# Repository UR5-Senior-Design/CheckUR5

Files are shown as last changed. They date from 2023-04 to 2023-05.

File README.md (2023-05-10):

# CheckUR5
## About
A Fall 2022 - Spring 2023 UTA Senior Design project that allows the UR5 collaborative robot arm to play a game of checkers with a human player.

Team CheckUR5:
- Nimita Uprety
- Patricia Rojas
- Hoang Ho
- Joanna Huynh
- Kevin Vu

Final demo video: https://www.youtube.com/watch?v=Sb-xevwk8ww

## Requirements
### Source Code
- [Main code](./main.py)
- [Arduino code](./arduino_magnet/arduino_magnet.ino)
- [Checkers code folder](./checkers)

### Physical Items
- UR5 collaborative robot arm
- Intel RealSense Depth Camera D435i
- 21 inch x 21 inch checkerboard
  - 0.5 inch border on each side
  - 2.5 inch x 2.5 inch squares
- 24 2 inch diameter [checker pieces](./designs/checker-piece-final.stl)
  - With washers or any magnetic material attached and ArUco markers on top
- Electromagnet gripper
  - Electromagnet circuit with Arduino Nano and MOSFET module
  - [Arduino code](./arduino_magnet/arduino_magnet.ino)
- Checker piece collection box

### Dependencies
- Linux distribution Ubuntu 22.04 LTS
- Python 3.x, we used 3.10.6
- OpenCV
- [RealSense SDK 2.0](https://dev.intelrealsense.com/docs/compiling-librealsense-for-linux-ubuntu-guide)
- [ur_rtde](https://pypi.org/project/ur-rtde/)
- pyserial

## Setup
Ensure the UR5 is connected to the same network as the PC that is running the code. Connect the camera and Arduino to SS USB ports.
- By default, the game uses `/dev/ttyUSB0/` as the Arduino port and `192.168.1.102` as the UR5's IP address. To change these, change line 26 in the [Game code](./checkers/game.py)

Movement logic of robot depends on its placement relative to the checkerboard and collection box. Each square's position is calculated based on the square designated as the top-left square and the distance difference between each square.

- To change where the top left square is, change `TOP_LEFT` in the [Robot code](./checkers/robot.py)
- To change where the collection box is, change `BOX_POS` in the [Robot code](./checkers/robot.py)

**The position values we used are based on the "Base" feature.**

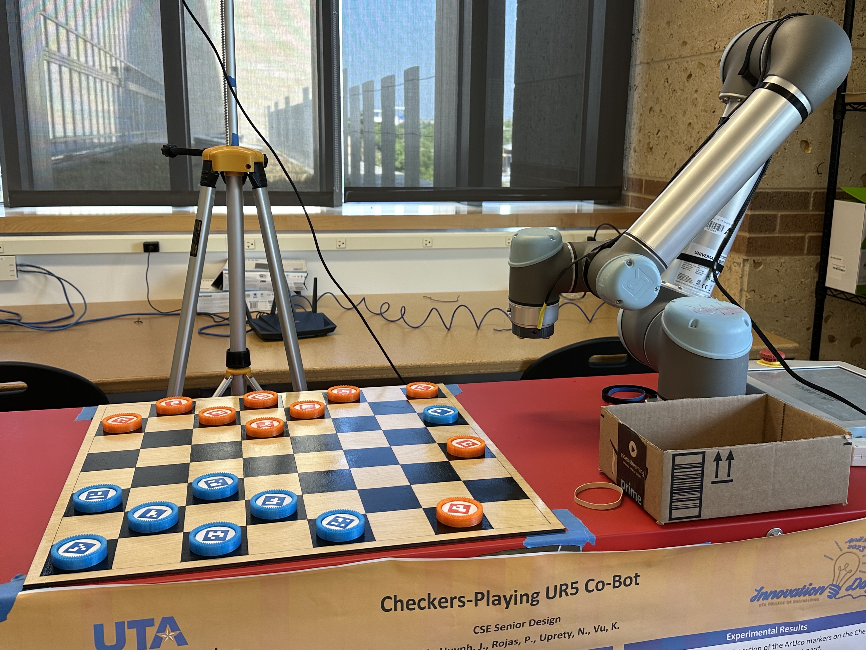
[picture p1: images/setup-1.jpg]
Project setup for playing checkers with the UR5 image 1

Project setup for playing checkers with the UR5 image 2
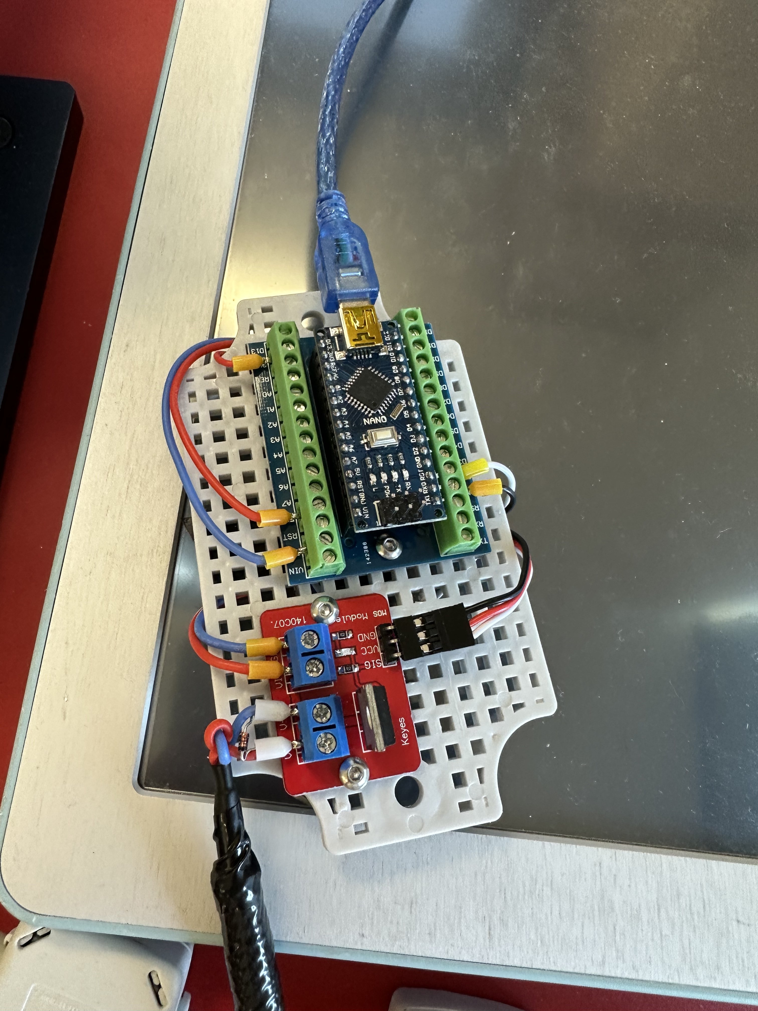
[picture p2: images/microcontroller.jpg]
The electromagnet circuit using the Arduino Nano and MOSFET module


## Playing the Game
1. Run [main.py](./main.py)
    - `python3 ./main.py`
2. Human player makes the first turn. Type `A` and press enter in the terminal to end the player's turn.
3. Enjoy!

## References
1. Techwithtim. (2020, September 3).“Techwithtim/Python-Checkers-AI/checkers: A checkers AI using the minimax algorithm.” Github, https://github.com/techwithtim/Python-Checkers-AI
2. Lindvig, A. P. (2022, October 31). Ur-rtde. PyPI. Retrieved April 7, 2023, from https://pypi.org/project/ur-rtde/ 
3. Söderby, K. (2023, March 9). Getting started with Arduino: Arduino documentation. Arduino Documentation | Arduino Documentation. Retrieved April 7, 2023, from https://docs.arduino.cc/learn/starting-guide/getting-started-arduino
4. UniversalRobots. (2012). Universal Robots User Manual Version 1.6. Universal Robots A/S.https://s3-eu-west-1.amazonaws.com/ur-support-site/17958/manual_en_UR5_CB2_1.6_US.pdf.

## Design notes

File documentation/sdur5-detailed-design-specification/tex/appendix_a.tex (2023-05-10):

% Include any additional documents (CAD design, circuit schematics, etc) as an appendix as necessary.
\subsection{CAD Models}
\begin{figure}[h!]
	\centering
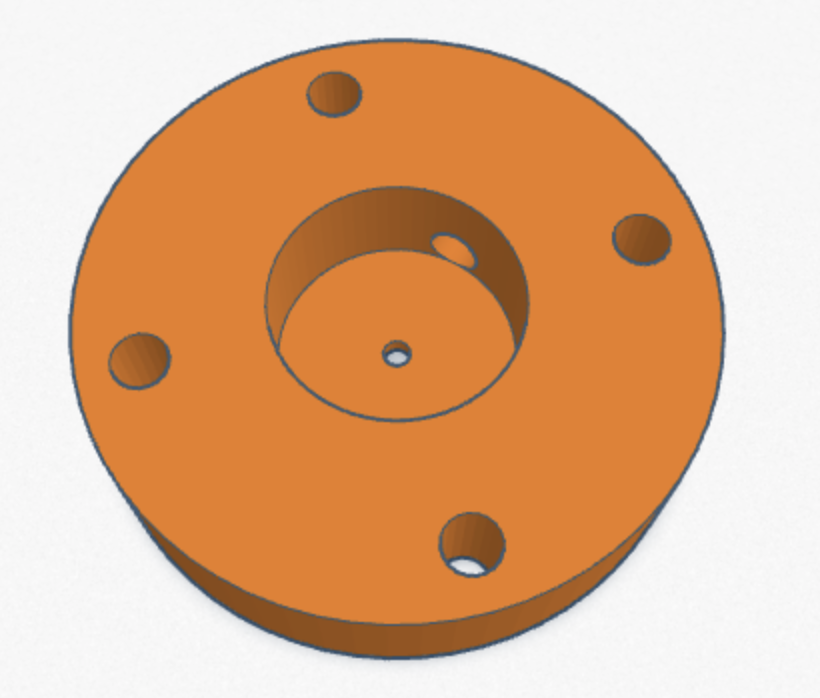
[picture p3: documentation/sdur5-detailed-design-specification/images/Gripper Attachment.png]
 	
 \caption{CAD Model of our Magnetic Gripper Attachment}
\end{figure}
\begin{figure}[h!]
	\centering
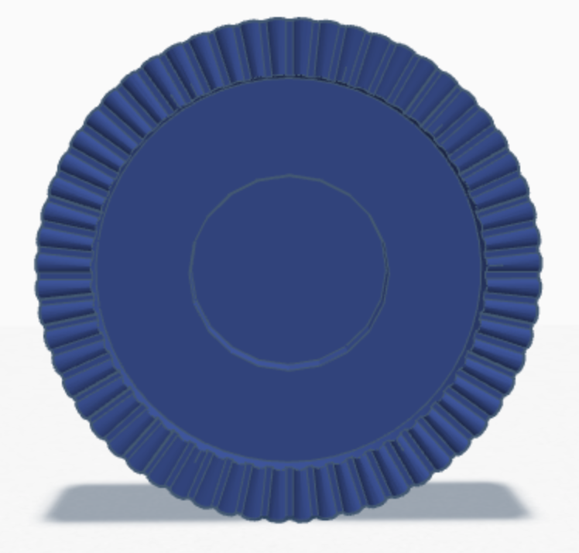
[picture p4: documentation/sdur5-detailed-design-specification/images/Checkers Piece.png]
 	
 \caption{CAD Model of our Regular Checkers Pieces}
\end{figure}
\begin{figure}[h!]
	\centering
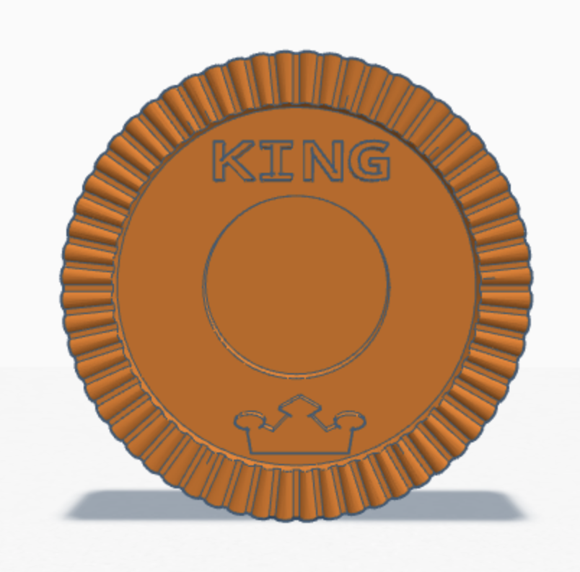
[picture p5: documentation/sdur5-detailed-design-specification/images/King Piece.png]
 	
 \caption{CAD Model of our King Checkers Pieces}
\end{figure}

\subsection{Circuit Schematics}
\begin{figure}[h!]
	\centering
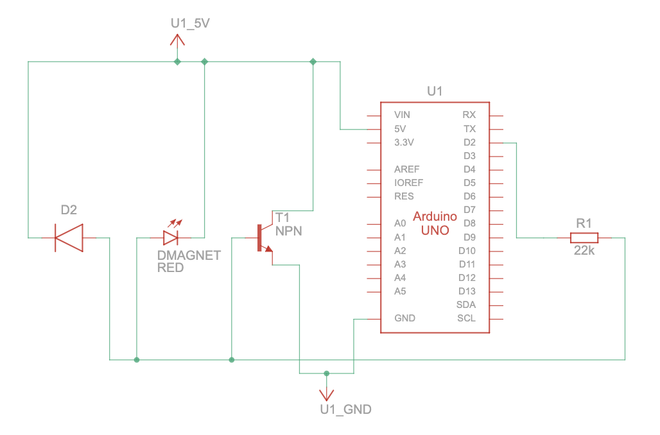
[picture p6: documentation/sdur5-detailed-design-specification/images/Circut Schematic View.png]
 	
 \caption{Schematic View of our Arduino \& Electromagnet setup}
\end{figure}
\begin{figure}[h!]
	\centering
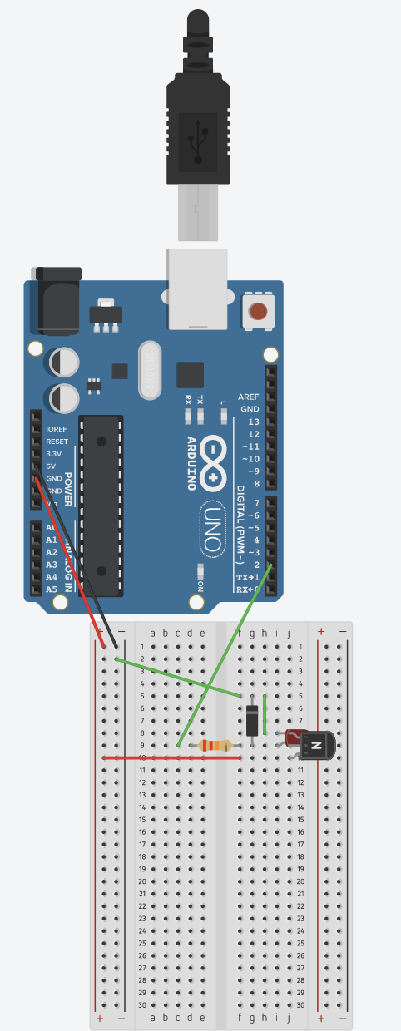
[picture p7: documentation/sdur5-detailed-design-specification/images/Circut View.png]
 	
 \caption{Circuit View of our Arduino \& Electromagnet setup}
\end{figure}

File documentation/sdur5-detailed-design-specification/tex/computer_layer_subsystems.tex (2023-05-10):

% In this section, the layer is described in terms of the hardware and software design. Specific implementation details, such as hardware components, programming languages, software dependencies, operating systems, etc. should be discussed. Any unnecessary items can be ommitted (for example, a pure software module without any specific hardware should not include a hardware subsection). The organization, titles, and content of the sections below can be modified as necessary for the project.
In this section, the Computer layer is described in detail. This layer consists of the HUD, GUI, and Software subsystems. Overall, the layer is responsible for communicating with the players information about the state of the game, sending the robot arm the actions it needs to take, and handling the decisions after each move.

\subsection{Layer Hardware}
% A description of any involved hardware components for the layer. For example, if each subsystem is a software process running on an embedded computer, discuss the specifics of that device here. Do not list a hardware component that only exists at the subsystem level (include it in the following sections).
The major hardware component of this layer is the computer itself. This computer is communicating to the UR5 robot arm through an Ethernet cable connected to the same router as the Ethernet cable connected to the UR5 control box. Additionally, as part of the computer, a monitor to display information to the player. A USB is also required to send to the Arduino the source code written to control the magnetic gripper.

\subsection{Layer Operating System}
% A description of any operating systems required by the layer.
The layer requires Linux distribution Ubuntu 22.04 LTS.

\subsection{Layer Software Dependencies}
% A description of any software dependencies (libraries, frameworks, etc) required by the layer.
 The layer will use the Python 3.10.6 programming language. It will also need to use the Arduino programming language to write the code to be executed on the Arduino that controls the magnetic gripper. Additionally, it is dependent on the Move Decision layer.

\subsection{HUD Subsystem}
% Descibe at a high level the purpose and basic design of this subsystem. Is it a piece of hardware, a class, a web service, or something else? Note that each of the subsystem items below are meant to be specific to that subystem and not a repeat of anything discussed above for the overall layer.
The Heads-Up Display (HUD) subsystem is a class that communicates with the Software subsystem of the Computer layer to receive information about the status of the game.The HUD subsystem displays to the user the status of the game and any information needed for the user. In this case the user is the Opponent layer. Information on the status of the game includes the current scores and a display of the game board on the computer monitor. This information is provided by the Software subsystem. Each time a player overtakes another player's checker piece, the score will be updated. When the physical game board changes, such as when a player moves a piece, this will also be reflected on the screen through the HUD.

\begin{figure}[h!]
	\centering
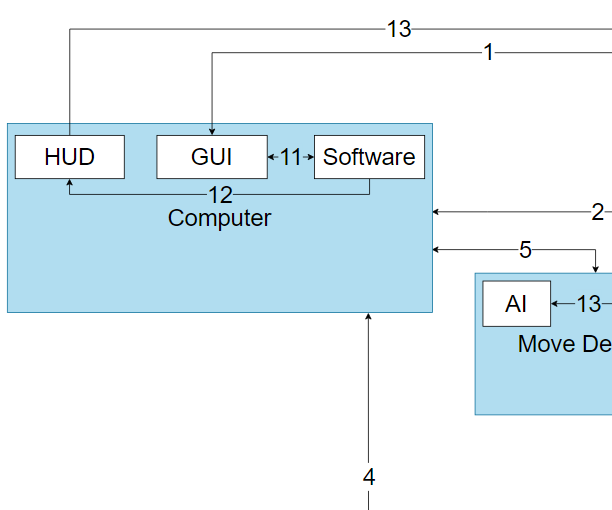
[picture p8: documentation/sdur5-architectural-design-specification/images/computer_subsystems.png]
 	
 \caption{Computer layer subsystems diagram}
\end{figure}

\subsubsection{Subsystem Hardware}
% A description of any involved hardware components for the subsystem.
A monitor connected to the computer to display game state status to the player.

% \subsubsection{Subsystem Operating System}
% A description of any operating systems required by the subsystem. removed because it is a repeat of things discussed above for the overall layer
% Linux distribution Ubuntu 22.04 LTS.

\subsubsection{Subsystem Software Dependencies}
% A description of any software dependencies (libraries, frameworks, design software for mechanical parts or circuits, etc) required by the subsystem.
This subsystem is dependent on the Software subsystem to receive information about the status of the game to display. It will also have software dependencies on GUI libraries such as PyQt5 or Tkinter.

\subsubsection{Subsystem Programming Languages}
% A description of any programming languages used by the subsystem.
The subsystem uses Python 3.10.6 as the programming language used.

\subsubsection{Subsystem Data Structures}
% A description of any classes or other data structures that are worth discussing for the subsystem. For example, data being transmitted from a microcontroller to a PC via USB should be first be assembled into packets. What is the structure of the packets?
N/A

\subsubsection{Subsystem Data Processing}
% A description of any algorithms or processing strategies that are worth discussing for the subsystem. If you are implementing a well-known algorithm, list it. If it is something unique to this project, discuss it in greater detail.
N/A

\subsection{GUI Subsystem}
% Descibe at a high level the purpose and basic design of this subsystem. Is it a piece of hardware, a class, a web service, or something else? Note that each of the subsystem items below are meant to be specific to that subystem and not a repeat of anything discussed above for the overall layer.
The Graphical User Interface (GUI) subsystem is a class that is the main interactive component between the Computer and Opponent layers. It communicates with the Software subsystem within the Computer layer for its inputs and outputs. The GUI displays buttons for the user (Opponent) to interact with. These buttons will be able to change the state of the game for purposes such as new game, restart game, and quit game. Each time the Opponent interacts with the GUI by clicking a corresponding button to a function, that button will send a mouse click signal for that button to the Software subsystem. This signals to the Software subsystem to execute the function associated with the button that is clicked. For example, if the user clicks a new game button, the software executes the processes needed to reset the state of the game and UR5 robot arm.

\subsubsection{Subsystem Hardware}
% A description of any involved hardware components for the subsystem.
A monitor connected to the computer to display the different options to the player. A mouse is also required for the player to interact with the GUI.

%\subsubsection{Subsystem Operating System}
% A description of any operating systems required by the subsystem. - removed because it is a repeat of things discussed above for the overall layer
% Linux distribution Ubuntu 22.04 LTS.

\subsubsection{Subsystem Software Dependencies}
% A description of any software dependencies (libraries, frameworks, design software for mechanical parts or circuits, etc) required by the subsystem.
This subsystem will have software dependencies on GUI libraries such as PyQt5 or Tkinter.

\subsubsection{Subsystem Programming Languages}
% A description of any programming languages used by the subsystem.
The subsystem uses Python 3.10.6 as the programming language used.

\subsubsection{Subsystem Data Structures}
% A description of any classes or other data structures that are worth discussing for the subsystem. For example, data being transmitted from a microcontroller to a PC via USB should be first be assembled into packets. What is the structure of the packets?
N/A

\subsubsection{Subsystem Data Processing}
% A description of any algorithms or processing strategies that are worth discussing for the subsystem. If you are implementing a well-known algorithm, list it. If it is something unique to this project, discuss it in greater detail.
N/A

\subsection{Software Subsystem}
% Descibe at a high level the purpose and basic design of this subsystem. Is it a piece of hardware, a class, a web service, or something else? Note that each of the subsystem items below are meant to be specific to that subystem and not a repeat of anything discussed above for the overall layer.
The Software subsystem is the main program for managing the checkers game itself and is behind the actions the UR5 Robot Arm will execute. This subsystem not only includes the source code itself, but also software packages needed for the program. The Software subsystem is responsible for handling events from the GUI. The subsystem also communicates with the UR5 robot arm through the Computer layer. The subsystem handles data on the status of the robot arm received from the robot arm itself. It also communicates to the robot arm what programmed actions it will need to perform. These actions will be determined by its interactions with the Move Decision layer which consists of the AI subsystem. The Software subsystem is also responsible for handling inputs from the Input Button/Device layer through the Computer layer.

\subsubsection{Subsystem Hardware}
% A description of any involved hardware components for the subsystem.
N/A

% \subsubsection{Subsystem Operating System}
% A description of any operating systems required by the subsystem. - removed because it is a repeat of things discussed above for the overall layer
%Linux distribution Ubuntu 22.04 LTS.

\subsubsection{Subsystem Software Dependencies}
% A description of any software dependencies (libraries, frameworks, design software for mechanical parts or circuits, etc) required by the subsystem.
The Software subsystem requires the ur\_rtde interface library to communicate with the UR5 robot arm. This library will allow us to write Python code to receive data from the UR5, and also control it. This is done using the RTDE Receive Interface API and RTDE Control Interface API from the library respectively. Documentation for the library can be found here: https://sdurobotics.gitlab.io/ur\_rtde/index.html. Controlling the UR5 includes communicating with the Move Execution layer and sending the commands to move the robot arm to a certain position. The subsystem is dependent on the Computer Vision and AI subsystems from the Move Decision layer to determine the commands it needs to send to the robot arm. It also needs this dependency to manage the checkers game and send the data required by the HUD subsystem. Moreover, it is also dependent on the GUI subsystem and Input Button/Device layer to listen to events from the player and handle them for the checkers game accordingly.

\subsubsection{Subsystem Programming Languages}
% A description of any programming languages used by the subsystem.
The subsystem uses Python 3.10.6 as the programming language used.

\subsubsection{Subsystem Data Structures}
% A description of any classes or other data structures that are worth discussing for the subsystem. For example, data being transmitted from a microcontroller to a PC via USB should be first be assembled into packets. What is the structure of the packets?
N/A

\subsubsection{Subsystem Data Processing}
% A description of any algorithms or processing strategies that are worth discussing for the subsystem. If you are implementing a well-known algorithm, list it. If it is something unique to this project, discuss it in greater detail.
N/A

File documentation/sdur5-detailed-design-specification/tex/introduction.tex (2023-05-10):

% Your introduction should provide a brief overview of the product concept and a reference to the requirement specification and architectural design documents in 1 or 2 paragraphs. The purpose is to provide the reader with the location of relevant background material that lead to the design details presented in this document.

The UR5 co-bot will be programmed to be able to play the interactive \& strategy-based game, checkers, against a human opponent. The robot will have an electropermanent magnetic attachment that will allow it to pick up and move the individual checkers pieces. The robot is not intended to beat the human opponent every time but rather just have the ability to play a full game of checkers against them. Our project aims to showcase the UR5 co-bot's abilities as a means of promoting the UT Arlington College of Engineering to prospective students through the means of an interactive demonstration.

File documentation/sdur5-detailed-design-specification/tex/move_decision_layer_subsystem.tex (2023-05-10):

 %In this section, the layer is described in terms of the hardware and software design. Specific implementation details, such as hardware components, programming languages, software dependencies, operating systems, etc. should be discussed. Any unnecessary items can be ommitted (for example, a pure software module without any specific hardware should not include a hardware subsection). The organization, titles, and content of the sections below can be modified as necessary for the project.
 In this section, we describe the move decision layer in detail. This layer consists of Artificial Intelligence and Computer Vision. Overall, this layer is responsible for one of the most important parts of this project that is the decision making process of the UR5 robot for the Checkers game. This does so by determining what commands to send to the robot arm.

\subsection{Layer Hardware}
%A description of any involved hardware components for the layer. For example, if each subsystem is a software process running on an embedded computer, discuss the specifics of that device here. Do not list a hardware component that only exists at the subsystem level (include it in the following sections).
This layer requires the computer to utilize artificial intelligence and computer vision aspects of the decision making.

\subsection{Layer Operating System}
%A description of any operating systems required by the layer.
The layer requires Linux distribution Ubuntu 22.04 LTS.

\subsection{Layer Software Dependencies}
%A description of any software dependencies (libraries, frameworks, etc) required by the layer.
The layer will use the Python 3.10.6 programming language. 

\subsection{Artificial Intelligence}
%Descibe at a high level the purpose and basic design of this subsystem. Is it a piece of hardware, a class, a web service, or something else? Note that each of the subsystem items below are meant to be specific to that subystem and not a repeat of anything discussed above for the overall layer.
The Artificial Intelligence communicates with the camera and Computer layer subsystems to make decisions for the UR5 robot arm.

\begin{figure}[h!]
	\centering
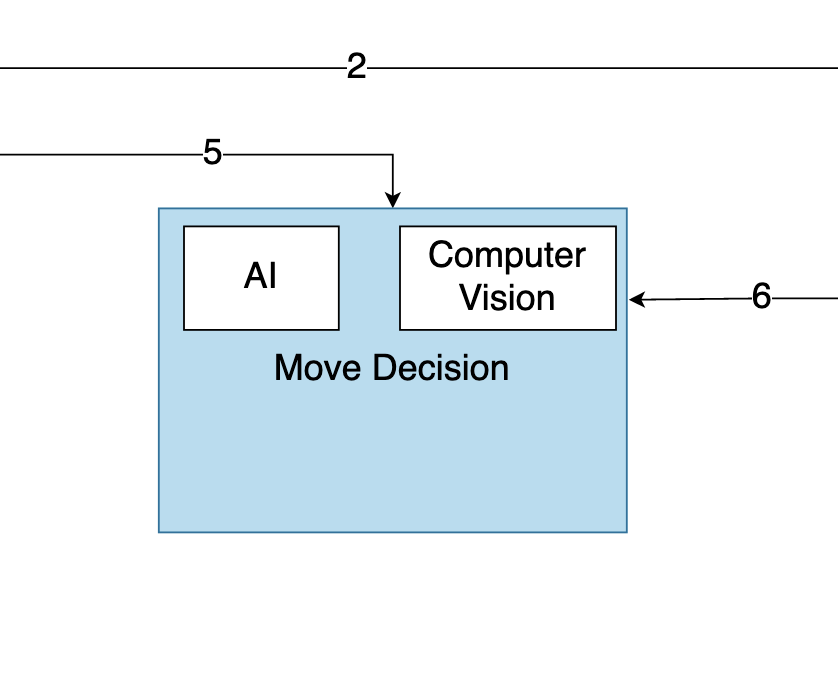
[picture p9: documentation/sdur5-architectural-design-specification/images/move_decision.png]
 	
 \caption{Example subsystem description diagram}
\end{figure}

\subsubsection{Subsystem Hardware}
%A description of any involved hardware components for the subsystem.
This subsystem requires the computer to utilize artificial intelligence aspect of the decision making.

\subsubsection{Subsystem Operating System}
%A description of any operating systems required by the subsystem.
The subsystem requires Linux distribution Ubuntu 22.04 LTS.

\subsubsection{Subsystem Software Dependencies}
%A description of any software dependencies (libraries, frameworks, design software for mechanical parts or circuits, etc) required by the subsystem.
The subsystem will use python libraries designed for artificial intelligence.

\subsubsection{Subsystem Programming Languages}
%A description of any programming languages used by the subsystem.
This subsystem will use the Python 3.10.6 programming language.

\subsubsection{Subsystem Data Structures}
%A description of any classes or other data structures that are worth discussing for the subsystem. For example, data being transmitted from a microcontroller to a PC via USB should be first be assembled into packets. What is the structure of the packets?
N/A

\subsubsection{Subsystem Data Processing}
%A description of any algorithms or processing strategies that are worth discussing for the subsystem. If you are implementing a well-known algorithm, list it. If it is something unique to this project, discuss it in greater detail.
N/A

\subsection{Computer Vision}
%Descibe at a high level the purpose and basic design of this subsystem. Is it a piece of hardware, a class, a web service, or something else? Note that each of the subsystem items below are meant to be specific to that subystem and not a repeat of anything discussed above for the overall layer.
The Computer Vision interacts with the frames received from the camera to determine the player's move.

% \begin{figure}[h!]
% 	\centering
%  	\includegraphics[width=0.60\textwidth]{images/subsystem}
%  \caption{Example subsystem description diagram}
% \end{figure}

\subsubsection{Subsystem Hardware}
%A description of any involved hardware components for the subsystem.
The subsystem will be using a camera to receive frames of the checkers position for both the players and will also use the computer for the computer vision process.

\subsubsection{Subsystem Operating System}
%A description of any operating systems required by the subsystem.
N/A

\subsubsection{Subsystem Software Dependencies}
%A description of any software dependencies (libraries, frameworks, design software for mechanical parts or circuits, etc) required by the subsystem.
This subsystem will use OpenCV and NumPy for the software dependencies.

\subsubsection{Subsystem Programming Languages}
%A description of any programming languages used by the subsystem.
This subsystem will use the Python 3.10.6 programming language.

\subsubsection{Subsystem Data Structures}
%A description of any classes or other data structures that are worth discussing for the subsystem. For example, data being transmitted from a microcontroller to a PC via USB should be first be assembled into packets. What is the structure of the packets?
N/A

\subsubsection{Subsystem Data Processing}
%A description of any algorithms or processing strategies that are worth discussing for the subsystem. If you are implementing a well-known algorithm, list it. If it is something unique to this project, discuss it in greater detail.
N/A

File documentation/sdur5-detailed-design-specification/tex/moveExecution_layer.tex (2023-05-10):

In this section, we describe the move execution layer. This layer is responsible for one of the key functionalities of our project which is the UR5 Robotic Arm's movement, which allows for the checkers game to take place between the user and the co-bot. The move execution layer is made up of three subsystems, the UR5 Robot Arm itself, the electromagnetic gripper, as well as an Arduino.

\subsection{Layer Hardware}
In terms of the Move Execution Layer the most heavily involved hardware component for this layer is the UR5 robotic arm itself. 

\subsection{Layer Operating System}
This layer utilizes Robot Operating System (ROS), although we do not primarily use ROS as we are primarily using Python to move our co-bot. ROS will be utilized to check the status of our robot's arm movements/coordinates at any given time.

\subsection{Layer Software Dependencies}
This layer will also utilize the Python 3.10.6 programming language. 

\begin{figure}[h!]
	\centering
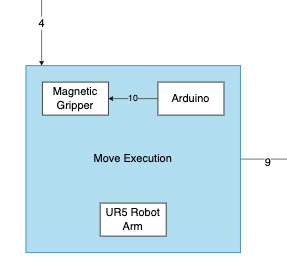
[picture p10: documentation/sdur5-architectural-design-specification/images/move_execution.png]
 	
 \caption{Move Execution subsystem description diagram}
\end{figure}

\subsection{UR5 Robot Arm}

The UR5 co-bot arm must be able to follow the instructions as asked by the software in order to hover over the correct location on the checker board. The robot must be able to move to fixed locations as predetermined by ROS and our custom software in order to not only move to specified pieces on the board but also to the collection box, and a waiting position.

The UR5 co-bot arm is responsible for the main mechanics of our project. As its ability to move to move to a spot on the board and pick up a piece and move it to another position is necessary so that the UR5 can play against its human oppponent.

\subsubsection{Subsystem Hardware}
In the UR5 Subsystem as well as the Move Execution Layer, the hardware component involved is the UR5 robotic arm itself.

\subsubsection{Subsystem Operating System}
The operating system required here is ROS.

\subsubsection{Subsystem Software Dependencies}
This subsystem layer will require a Universal Robots Python library so that we can control the co-bots movements through python scripts. The Python library we intend on using for this is ur\_rtde.

\subsubsection{Subsystem Programming Languages}
The UR5 subsystem requires the Python 3.10.6 programming language.

\subsubsection{Subsystem Data Structures}
The pre-recorded coordinates of our robot's movements will be saved into a multi-dimensional array so that our robot will have a list of saved positions to go to. The decision on where to go is determined by our Move Decision layer.

\subsubsection{Subsystem Data Processing}
N/A

\subsection{Magnetic Gripper}
The Magenetic subsystem of our Move Execution Layer is responsible for the UR5 robotic arm's ability to "pick-up" each checkers piece. This subsystem is integral to the project as a whole because without it the pieces will not be moved and the checkers game cannot be played.

\subsubsection{Subsystem Hardware}
This subsystem requires more hardware components than some of our other subsystems. It consists of an Arduino, an electromagnet, transistor NPN(2N3904), diode(1N4148), 22K Ω resistor, wires, breadboard, as well as a 3D printed attachement so that it can be screwed into the UR5 arm.

\subsubsection{Subsystem Operating System}
N/A

\subsubsection{Subsystem Software Dependencies}
This subsystem layer requires the Arduino 2.0.3 IDE. As that is needed for us to provide python scripts to Arduino which in turn will power our electromagnet.

\subsubsection{Subsystem Programming Languages}
The UR5 subsystem requires the Python 3.10.6 programming language.

N/A

\subsubsection{Subsystem Data Processing}
N/A

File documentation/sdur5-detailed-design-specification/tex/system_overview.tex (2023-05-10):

% This section should reintroduce the full data flow diagram from the architectural specification, and discuss at a high level the purpose of each layer. You do not need to include a subsection for each layer, a 1 - 2 paragraph recap is sufficient.
\begin{flushleft}
The system for our product is currently simplified into 4 layers and 3 high-level components. Each layer/component will interact with one another in different ways.
\end{flushleft}
\begin{flushleft}
The Opponent is the person that will be going against the robot during the checkers game. The Input Device is one of the ways the opponent will be able to facilitate the progression of the checkers match. The camera is the component that acts as the eyes into the real world for our system. The Move Decision layer is the layer that will make all of the move decisions that the robot will make. This layer consists of Computer Vision and AI. The Computer layer is the central piece of our system. This layer acts as the facilitator of the checkers match, and receives input from the Opponent to progress the match, sends signals to the AI layer to grab board state and make a move, and signals the UR5 Robot Arm layer to execute those moves. The Move Execution layer is the layer that will physically execute the moves that our system will make during a checkers match with the robot arm and related parts. And finally, The External Components layer is composed of all of the physical checkers board game pieces. Both the Opponent component and the Move Execution layer physically interact with the External Components layer when they have made their move decisions to progress the match.
\end{flushleft}

\begin{figure}[h!]
	\centering
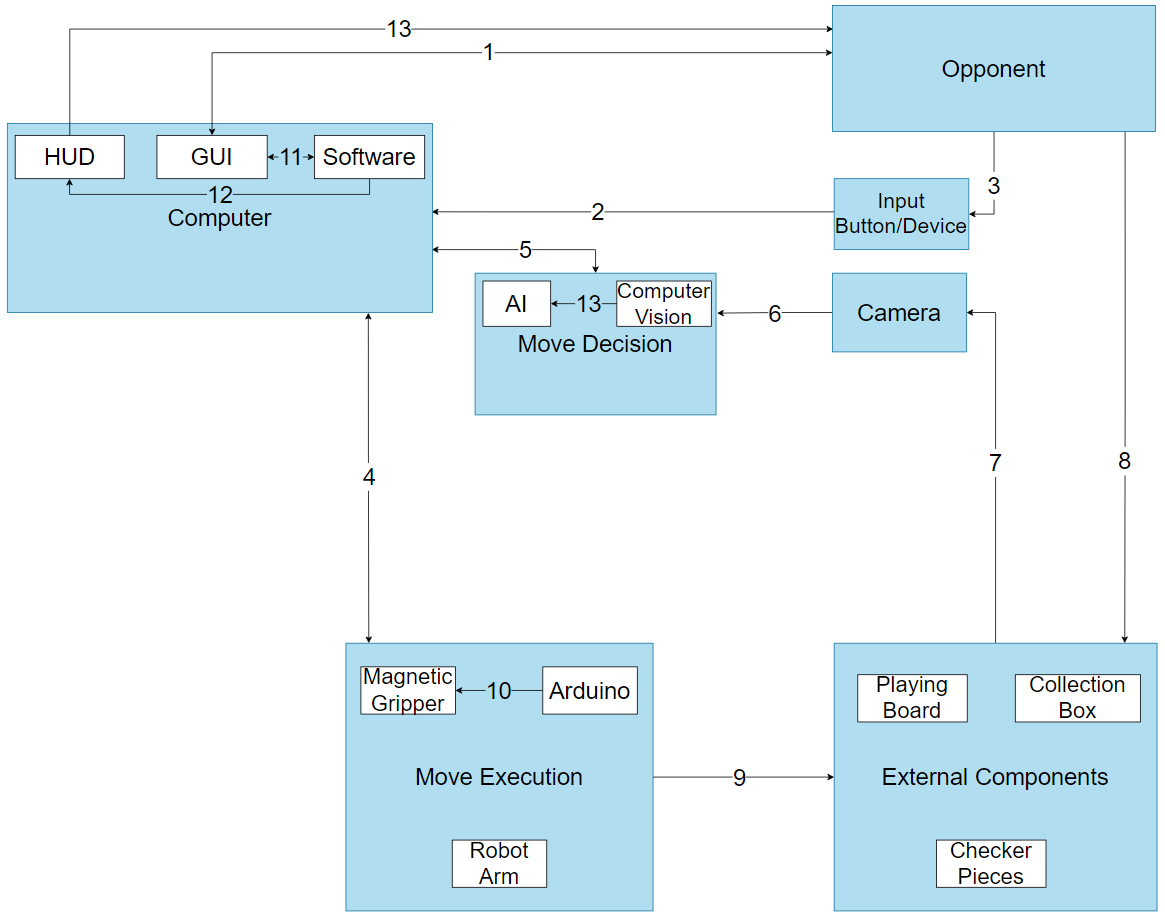
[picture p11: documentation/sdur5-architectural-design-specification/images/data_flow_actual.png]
 	
 \caption{System architecture}
\end{figure}

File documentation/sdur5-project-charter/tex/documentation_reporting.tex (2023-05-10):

%%% In this section, you will describe all of the various artifacts that you will generate and maintain during the project life cycle. Describe the purpose of each item below, how the content will be generated, where it will be stored, how often it will be updated, etc. Replace the default text for each section with your own description. Reword this paragraph as appropriate.

\subsection{Major Documentation Deliverables}
\subsubsection{Project Charter}
The project charter is intended to communicate Team UR5's understanding and research on the project. It is the current list of commitments the team will be making. The initial version of the document will be delivered October 3, 2022. The final version will be delivered during the second semester in May 2023. This document will be maintained and updated after every sprint as needed, and when the sponsor approves of these changes.

% Describe how this document will be maintained and updated (how often, under what circumstances, etc.). When will the initial version be delivered? When will the final version be delivered?
https://www.overleaf.com/project/631b8af69f1ea6c375d502b0
\subsubsection{System Requirements Specification}
The Systems Requirements Specification will be maintained and updated during every sprint as features are added or with further understanding of the technology. The initial version of this document will be delivered October 24, 2022. The final version will be delivered during the second semester in May 2023.

% Describe how this document will be maintained and updated (how often, under what circumstances, etc.). When will the initial version be delivered? When will the final version be delivered?

\subsubsection{Architectural Design Specification}
The Architectural Design Specification will be maintained and updated as needed during every sprint especially when there are changes in design or clarifications. The initial version of this document will be delivered November 14, 2022. The final version will be delivered during the second semester in May 2023.

% Describe how this document will be maintained and updated (how often, under what circumstances, etc.). When will the initial version be delivered? When will the final version be delivered?

\subsubsection{Detailed Design Specification}
The Detailed Design Specification will be maintained and updated as needed during every sprint especially when there are changes in design or clarifications. The initial version of this document will be delivered within the first quarter of 2023. The final version will be delivered during the second semester in May 2023.

% Describe how this document will be maintained and updated (how often, under what circumstances, etc.). When will the initial version be delivered? When will the final version be delivered?

\subsection{Recurring Sprint Items}
\subsubsection{Product Backlog}
Items will be added to the product backlog as the System Requirements Specification document is updated. These items will be prioritized based on customer needs and feasibility of the requirement for the current point in time. Team vote and feedback will also be taken into consideration. Jira Software by Atlassian will be used to maintain and work collaboratively on the product backlog.

% How will items be added to the product backlog from the SRS? How will these items be prioritized? Who makes the decision (product owner, group vote, etc.)? What software will be used to maintain and share the product backlog with team members and stakeholders?

\subsubsection{Sprint Planning}
Each sprint will be planned based on documentation and feature implementation deadlines. Team meetings will be held after each sprint to determine the sprint goals. There will be 4 sprints for the first semester and 4 sprints for the second semester, totalling 8 sprints for both semesters.

% How will each sprint plan be planned? How many sprints will there be (you need to look at the schedules for this course and previous Senior Design II courses during the appropriate semesters to figure this out).

\subsubsection{Sprint Goal}
The team will meet and discuss sprint goals. These sprint goals will be decide as a team. Our customer Christopher McMurrough will be involved in the process as needed through scheduled meetings.

% Who decides the sprint goal? How will you involve your customer in this process?

\subsubsection{Sprint Backlog}
Team discussion will be held to determine which product backlog items will make their way into the sprint backlog. The backlog will be maintained using Jira Software developed by Atlassian.

% Who decides which product backlog items make their way into the sprint backlog? How will the backlog be maintained (collaboration software, a "scrum board", etc.)?

\subsubsection{Task Breakdown}
Each team member will voluntarily claim a task, otherwise it will be random. Time spent on tasks will be documented using Jira Software.

% How will individual tasks be assigned from the sprint backlog? Will it be up to each team member to voluntarily claim a task, or will it come from the product owner? How will time spent on tasks be documented?

\subsubsection{Sprint Burn Down Charts}
The burn down charts will allow the team to track the progress of the project. Currently, using Jira Software will automatically generate the burn down charts for each sprint. Each individual team member is responsible for manually updating the effort and time spent as they complete each assigned task. Jira Software will also be able to access all of this. In addition to the Jira log, Microsoft Excel will be used to manually create the burn down charts in case members don't update on Jira. See Figure 2 and 3 for examples.

\begin{figure}[h!]
    \centering
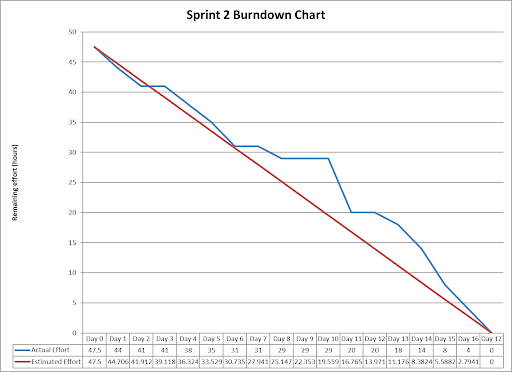
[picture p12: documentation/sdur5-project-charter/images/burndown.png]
    
    \caption{Example sprint burn down chart}
\end{figure}

\begin{figure}[h!]
    \centering
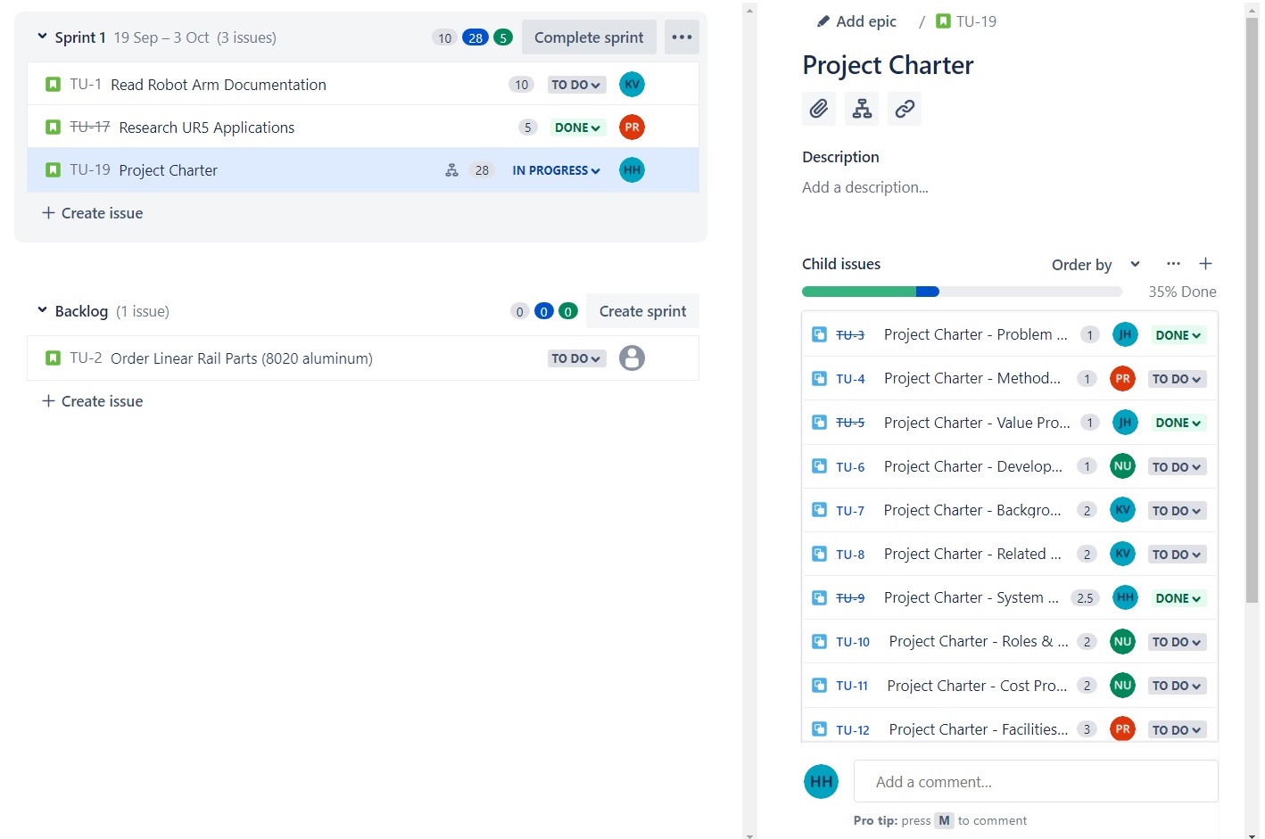
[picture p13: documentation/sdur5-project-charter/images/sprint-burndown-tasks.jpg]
    
    \caption{Example task tracking}
\end{figure}

% Who will be responsible for generating the burn down charts for each sprint? How will they be able to access the total amount of effort expended by each individual team member? What format will the burn down chart use (include an example burn down chart below).

\subsubsection{Sprint Retrospective}
The sprint retrospective will be handled as a team during team meetings. This discussion will happen after each sprint review presentation at the end of each sprint. What went well, and what is needed to be adjusted will be documented as a team before the next sprint plan meeting.

% How will the sprint retrospective be handled as a team? When will this discussion happen after each sprint? What will be documented as a group and as individuals, and when will it be due?

\subsubsection{Individual Status Reports}
Each individual member will primarily report the tasks assigned to them and the time spent on each task for each sprint. Individuals can also include in their report any concerns or issues that may be addressed for future sprints.

% What sort of status will be reported by each individual member, and how often will it be reported? What key items will be contained in the report?

\subsubsection{Engineering Notebooks}
%%% notes, status reports, budgeting, sprint info
% The engineering notebook may contain any project notes, status reports, budgeting, sprint information, etc. It will be updated every week by each team member at minimum. The minimum amount of pages that will be completed will be 1 page for each sprint period. These sprint periods are around 2 weeks long. Any team member that is not the author will sign as a "witness" for each page.

% How often will the engineering notebook be updated, at a minimum, by each team member? What is the minimum amount of pages that will be completed for each interval, and how long will that interval be? How will the team keep each member accountable? Who will sign of as a "witness" for each ENB page?

\subsection{Closeout Materials}
\subsubsection{System Prototype}
Included in the final system prototype will be all major components (computer software, UR5, sensors, checkerboard, etc.) to demonstrate a game with the UR5.

% What will be included in the final system prototype? How and when will this be demonstrated? Will there be a Prototype Acceptance Test (PAT) with your customer? Will anything be demonstrated off-site? If so, will there be a Field Acceptance Test (FAT)?

\subsubsection{Project Poster}
Included on the project poster will be an overview, methodology and design, and results. Poster dimensions will be 32 inches tall by 40 inches wide.

% What will be included on the poster, what will be the final dimensions, and when will it be delivered?

% \subsubsection{Web Page}
% The project web page will have the project's overview, design, results, and document deliverables. The web page will be accessible to the public. When the web page will be delivered and updated is still to be decided.

% What will be included on the project web page? Will it be accessible to the public? When will this be delivered? Will it be updated throughout the project, or just provided at closeout (at a minimum, you need to provide a simple web page at the end).

\subsubsection{Demo Video}
Shown in the demo video will be the robot playing a game with a human. B-reel footage will be recorded throughout project implementation to show progress and different features.

% What will be shown in the demo video(s)? Will you include a B-reel footage for future video cuts? Approximately how long will the video(s) be, and what topics will be covered?

\subsubsection{Source Code}
The source code will be maintained on GitHub using the Git version control system. The source code will also be publicly available to the customer through GitHub. License terms are still to be decided, but still likely be listed in a single ReadMe file.

% How will your source code be maintained? What version control system will you adopt? Will source code be provided to the customer, or binaries only? If source code is provided, how will it be turned over to the customer? Will the project be open sourced to the general public? If so, what are the license terms (GNU, GPL, MIT, etc.). Where will the license terms be listed (in each source file, in a single readme file, etc.).

\subsubsection{Source Code Documentation}

The team plans to write a README for documentation and setup instructions for future users. The team also plans to potentially look into using Doxygen or Pydocs to generate the documentation. The format of the final documentation is still to be decided, however it is likely it will provided as a PDF or HTML file.

% The team plans to look into using Doxygen or Pydocs to generate the documentation. The format of the final documentation is still to be decided, however it is likely it will provided as a PDF or HTML file.

% What documentation standards will be employed? Will you use tools to generate the documentation (Doxygen, Javadocs, etc.). In what format will the final documentation be provided (PDF, browsable HTML, etc.)?

\subsubsection{Hardware Schematics}
The project will involve the UR5 Robot Arm. This robot arm will need a gripper for picking up pieces. In addition to that, a camera will be needed for the robot to detect the state of the game board, determine its next move, and move its pieces. The rest of the project involves python scripts.

% Will you be creating printed circuit boards (PCBs) or wiring components together? If so, list each applicable schematic and what sort of data it will contain (PCB layout, wiring diagram, etc.). If your project is purely software, omit this section.

\subsubsection{CAD files}
The project will need custom checker pieces if the UR5 plans to use a magnetic gripper to pick up the pieces. The FabLab at UTA has software support for SketchUp, Meshmixer, Tinkercad, Fusion 360, and SolidWorks. Currently, the plan is to use the free, online 3D modeling program Tinkercad to make the pieces. Blender could also be another free option to use outside of the software supported in the FabLab. The CAD files will be saved in STL file format to work with the 3D printers available in the FabLab at UTA.

% Will the project involve any mechanical design, such as 3D printed or laser-cut parts? If so, what software will you use to generate the files and what file formats will you provide in your closeout materials (STL, STEP, OBJ, etc.). If your project is purely software, omit this section.

\subsubsection{Installation Scripts}
There are currently no plans to provide installation scripts. At the moment, instructions are planned to be found in the ReadMe file on the GitHub repository.

% How will the customer deploy software to new installations? Will you provide installation scripts, install programs, or any other tools to improve the process? Will there be multiple scripts provided (perhaps separate scripts for the graphical front end and back end server software)? 

% \subsubsection{User Manual}
% A digital user manual will be provided for the customer. This digital user manual can also be printed.

% Will you customer need a printed or digital user manual? Will they need a setup video? Decide now what will be provided and discuss.

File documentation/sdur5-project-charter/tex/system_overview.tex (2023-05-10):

The UR5 co-bot will be able to play a game of checkers against a human opponent. In order for the robot to do this, the robot arm will need a gripper and a camera. The gripper will be needed to pick up checker pieces. This gripper could be magnetic or a suction cup. In the case of a magnetic gripper, the checker pieces themselves will need to also be magnetic. The robot arm will also need to be paired with a camera in order to see and detect the checkerboard and its pieces. This is so the robot arm can determine the current state of the game, and determine the next optimal move for a piece to take. The computer will communicate with the robot arm and issue commands for it to make a particular move. Shown in Figure 1 is a high-level view of the implementation.

\begin{figure}[h!]
    \centering
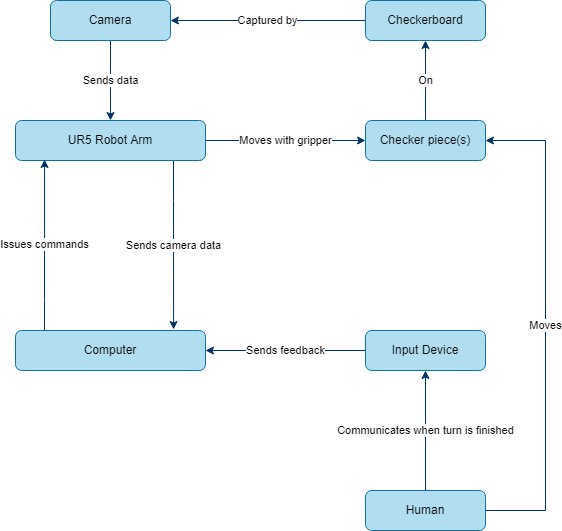
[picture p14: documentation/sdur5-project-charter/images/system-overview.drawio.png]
    
    \caption{System Overview}
\end{figure}

As is illustrated in Figure 1, when the human player makes a move, the human must use some input device to communicate to the computer that they have completed their turn and it is now the UR5's turn to make a move. This input device could be a simple external button, or the computer keyboard. The computer is responsible for being the interface that communicates with the robot arm on what move it should make, how it should move, and any other commands needed to control it. Additionally, the computer will process the data received from the camera on the robot arm utilizing computer vision.

% Explain, at a high level, how you will implement a solution to the problem. Include a diagram of major components to the system (not a full architectural design, but a high level overview of the major system components and how a user or external system might interface). Avoid specific implementation details (operating system, programming languages, etc.). This section should occupy at least 1 full page.

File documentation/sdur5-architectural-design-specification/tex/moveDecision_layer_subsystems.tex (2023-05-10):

%In this section, the layer is described in some detail in terms of its specific subsystems. Describe each of the layers and its subsystems in a separate chapter/major subsection of this document. The content of each subsystem description should be similar. Include in this section any special considerations and/or trade-offs considered for the approach you have chosen.
In this section, we describe the move decision layer. This layer is responsible for the decision making process of the UR5 robot for the Checkers game.
\subsection{Artificial Intelligence}
%This section should be a general description of a particular subsystem for the given layer. For most subsystems, an extract of the architectural block diagram with data flows is useful. This should consist of the subsystem being described and those subsystems with which it communicates.
The Artificial Intelligence communicates with the camera and Computer layer subsystems to make decisions for the UR5 robot arm.
\begin{figure}[h!]
	\centering
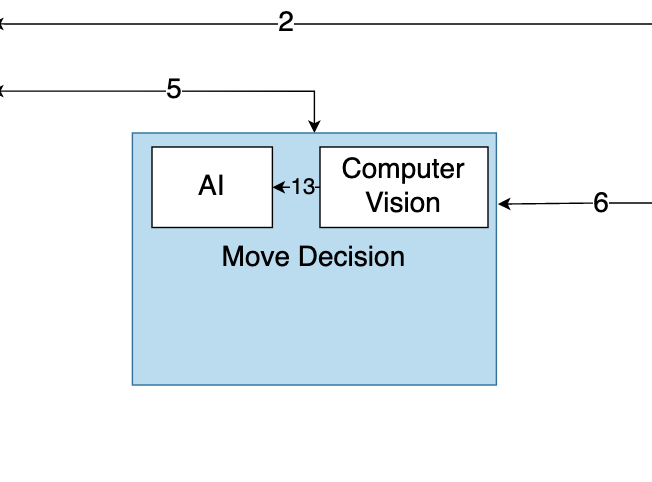
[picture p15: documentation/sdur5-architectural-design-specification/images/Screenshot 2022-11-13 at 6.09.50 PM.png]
 	
 \caption{Move decision layer subsystems diagram}
\end{figure}

\subsubsection{Assumptions}
%Any assumptions made in the definition of the subsystem should be listed and described. Pay particular attention to assumptions concerning interfaces and interactions with other layers.
N/A

\subsubsection{Responsibilities}
%Each of the responsibilities/features/functions/services of the subsystem as identified in the architectural summary must be expanded to more detailed responsibilities. These responsibilities form the basis for the identification of the finer-grained responsibilities of the layer's internal subsystems. Clearly describe what each subsystem does.
The Artificial Intelligence calculates the next move for the Computer. It compares the best move by looking at the next two to three steps ahead by the appropriate algorithm. It also determines any invalid moves by the player.  

\subsubsection{Artificial Intelligence Interfaces}
%Each of the inputs and outputs for the subsystem are defined here. Create a table with an entry for each labelled interface that connects to this subsystem. For each entry, describe any incoming and outgoing data elements will pass through this interface.
Details in Table 5 show the incoming and outgoing data elements.
\begin {table}[H]
\caption {Subsystem interfaces} 
\begin{center}
    \begin{tabular}{ | p{1cm} | p{6cm} | p{3cm} | p{3cm} |}
    \hline
    ID & Description & Inputs & Outputs \\ \hline
    \#5 & Signal from the computer & \pbox{3cm}{N/A} & \pbox{3cm}{N/A}  \\ \hline
    \end{tabular}
\end{center}
\end{table}

\subsection{Computer Vision}
%This section should be a general description of a particular subsystem for the given layer. For most subsystems, an extract of the architectural block diagram with data flows is useful. This should consist of the subsystem being described and those subsystems with which it communicates.
The Computer Vision interacts with the frames received from the camera to determine the player's move.

\subsubsection{Assumptions}
%Any assumptions made in the definition of the subsystem should be listed and described. Pay particular attention to assumptions concerning interfaces and interactions with other layers.
N/A

\subsubsection{Responsibilities}
%Each of the responsibilities/features/functions/services of the subsystem as identified in the architectural summary must be expanded to more detailed responsibilities. These responsibilities form the basis for the identification of the finer-grained responsibilities of the layer's internal subsystems. Clearly describe what each subsystem does.
It successfully identifies the movements of the Checkers pieces. It also identifies the current locations on the Checkers board.

\subsubsection{Subsystem Interfaces}
%Each of the inputs and outputs for the subsystem are defined here. Create a table with an entry for each labelled interface that connects to this subsystem. For each entry, describe any incoming and outgoing data elements will pass through this interface.
Details in Table 6 show the incoming and outgoing data elements.
\begin {table}[H]
\caption {Computer Vision interfaces} 
\begin{center}
    \begin{tabular}{ | p{1cm} | p{6cm} | p{3cm} | p{3cm} |}
    \hline
    ID & Description & Inputs & Outputs \\ \hline
   \#13 & Send input to Artificial Intelligence & \pbox{3cm}{Computer Vision input} & \pbox{3cm}{Checkers Move}  \\ \hline
    \#6 & Receives camera frames & \pbox{3cm}{Camera Frames} & \pbox{3cm}{Checkers board movement}  \\ \hline
    \end{tabular}
\end{center}
\end{table}

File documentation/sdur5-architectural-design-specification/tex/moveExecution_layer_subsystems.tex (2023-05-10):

In this section, we describe the move execution layer. This layer is responsible for one of the key functionalities of our project which is the UR5 Robotic Arm's movement, which allows for the checkers game to take place between the user and the co-bot. The move execution layer is made up of three subsystems, the UR5 Robot Arm itself, the electromagnetic gripper, as well as an Arduino.

\subsection{UR5 Robot Arm}
\begin{figure}[h!]
	\centering
 	
 \caption{Move execution layer subsystems diagram}
\end{figure}

\subsubsection{Assumptions}
Here our biggest assumption is the fact that the UR5 arm has already been connected to the software functionality and therefore can be programmed to make specific moves.

\subsubsection{Responsibilities}
The UR5 co-bot arm must be able to follow the instructions as asked by the software in order to hover over the correct location on the checker board. The robot must be able to move to fixed locations as predetermined by ROS and our custom software in order to not only move to specified pieces on the board but also to the collection box, and a waiting position.

\subsubsection{Subsystem Interfaces}
\begin {table}[H]
\caption {UR5 Robot Arm interfaces} 
\begin{center}
    \begin{tabular}{ | p{1cm} | p{6cm} | p{3cm} | p{3cm} |}
    \hline
    ID & Description & Inputs & Outputs \\ \hline
    \#4 & Receive input from computer/software & \pbox{3cm}{Location of next move} & \pbox{3cm}{UR5 Arm will move to expected location}  \\ 
    \hline
    \end{tabular}
\end{center}
\end{table}

\subsection{Arduino}
\subsubsection{Assumptions}
N/A

\subsubsection{Responsibilities}
The Arduino system has the primary responsibility of being the micro-controller of our magnetic gripper. We will be integrating the Arduino into our software so that we can have the ability to turn our electromagnet on and off whenever we are moving our checkers pieces around.

\subsubsection{Subsystem Interfaces}
\begin {table}[H]
\caption {Arduino interfaces} 
\begin{center}
    \begin{tabular}{ | p{1cm} | p{6cm} | p{3cm} | p{3cm} |}
    \hline
    ID & Description & Inputs & Outputs \\ \hline
    \#4 & Receive input from computer/software & \pbox{3cm}{Signal indicating on/off} & \pbox{3cm}{Arduino will store on/off signal to send to magnetic gripper}  \\ \hline
    \#10 & Send signal to  magnetic gripper & \pbox{3cm}{Stored on/off signal in Arduino} & \pbox{3cm}{Send on/offsignal to magnetic gripper}  \\ 
    \hline
    \end{tabular}
\end{center}
\end{table}

\subsection{Magnetic Gripper}
\subsubsection{Assumptions}
We will assume that the magnetic gripper has been attached to the "hand" or tip of the UR5 Robot Arm, via a base that has been 3D printed.

\subsubsection{Responsibilities}
The Magnetic Gripper allows for game play interaction to take place as it will be the component that physically picks up and releases each individual checkers piece throughout the game.

\subsubsection{Subsystem Interfaces}
\begin {table}[H]
\caption {Magnetic Gripper interfaces}
\begin{center}
    \begin{tabular}{ | p{1cm} | p{6cm} | p{3cm} | p{3cm} |}
    \hline
    ID & Description & Inputs & Outputs \\ \hline
    \#10 & Receive signal from Arduino & \pbox{3cm}{On/off signal from Arduino} & \pbox{3cm}{Magnetic gripper will turn on/off accordingly}  \\ 
    \hline
    \end{tabular}
\end{center}
\end{table}

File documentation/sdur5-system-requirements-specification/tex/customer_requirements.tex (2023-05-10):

% Include a header paragraph specific to your product here. Customer requirements are those required features and functions specified for and by the intended audience for this product. This section establishes, clearly and concisely, the "look and feel" of the product, what each potential end-user should expect the product do and/or not do. Each requirement specified in this section is associated with a specific customer need that will be satisfied. In general Customer Requirements are the directly observable features and functions of the product that will be encountered by its users. Requirements specified in this section are created with, and must not be changed without, specific agreement of the intended customer/user/sponsor.

% \subsection{Requirement Name}
% \subsubsection{Description}
% A detailed description of the feature/function that satisfies the requirement. For example: \textit{The GUI background will be slate blue. This specific color is required in order to ensure that the GUI matches other similar software products offered by the customer. Slate blue is specified as \#007FFF, using six-digit hexadecimal color specification.} It is acceptable and advisable to include drawings/graphics in the description if it aids understanding of the requirement.
% \subsubsection{Source}
% The source of the requirement (e.g. customer, sponsor, specified team member (by name), federal regulation, local laws, CSE Senior Design project specifications, etc.)
% \subsubsection{Constraints}
% A detailed description of realistic constraints relevant to this requirement. Economic, environmental, social, political, ethical, health \& safety, manufacturability, and sustainability should be discussed as appropriate.
% \subsubsection{Standards}
% A detailed description of any specific standards that apply to this requirement (e.g. \textit{NSTM standard xx.xxx.x. color specifications \cite{Rubin2012}}. Standards exist for practically everything (ATC standard fuses, IEEE 802.15.4 embedded wireless, TLS 1.3 encryption, etc.), so be sure that you research and document which ones will be followed in meeting this requirement.
% \subsubsection{Priority}
% The priority of this requirement relative to other specified requirements. Use the following priorities:
% \begin{itemize}
% \item Critical (must have or product is a failure)
% \item High (very important to customer acceptance, desirability)
% \item Moderate (should have for proper product functionality);
% \item Low (nice to have, will include if time/resource permits)
% \item Future (not feasible in this version of the product, but should be considered for a future release).
% \end{itemize}

% \subsection{Requirement Name}
% \subsubsection{Description}
% Detailed requirement description...
% \subsubsection{Source}
% Source
% \subsubsection{Constraints}
% Detailed description of applicable constraints...
% \subsubsection{Standards}
% List of applicable standards
% \subsubsection{Priority}
% Priority

The customers of the UR5 Checkers-Playing Co-bot include, but are not limited to, the project sponsor, the developers, peers, UTA College of Engineering, and prospective students. This section establishes what the end-user should expect with the product. The co-bot will come with a custom-made checkerboard and custom-made checkers pieces to ensure that the physical components of the game are large enough to be detected by the UR5 co-bot's magnetic electro-permanent gripper. The product will also include a collection box for both the user and robot to deposit the checkers pieces during the match. The user will have control over terminating or resetting the match.   

\subsection{The product shall have a custom-made checkerboard.}
\subsubsection{Description}
The checkerboard will be constructed of a 18 inch by 18 inch wooden board and be custom-painted. It is custom-made to ensure that the size of the checkerboard and checkers pieces are large enough to be easily detected and grasped by the robot arm.
\subsubsection{Source}
Kevin Vu
\subsubsection{Constraints}
The custom board must be small enough to comfortably fit the UR5 stand base, and the squares must be large enough to fit the checkers pieces.
\subsubsection{Standards}
N/A
\subsubsection{Priority}
Critical

\subsection{The product shall have custom-made checker pieces.}
\subsubsection{Description}
These checker pieces will be 3D printed and will have a small magnet contained within them for the robot to grip the piece.
\subsubsection{Source}
Hoang Ho
\subsubsection{Constraints}
The checker pieces need to have a hole cut out for the washers to be inserted in them for easy pickup by the magnet in the robot arm. 
\subsubsection{Standards}
N/A
\subsubsection{Priority}
Critical

\subsection{The product shall have a piece collection box.}
\subsubsection{Description}
The box will hold the checkers pieces that the robot arm picks up throughout a checkers match. Additionally, when storing away the game, the checkers pieces can go in here.
\subsubsection{Source}
Kevin Vu
\subsubsection{Constraints}
The box must be in reach of the UR5 robot arm during game play to drop off its checker pieces.
\subsubsection{Standards}
N/A
\subsubsection{Priority}
High

\subsection{The UR5 robot arm shall have a magnetic electro-permanent gripper.}
\subsubsection{Description}
This gripper will have the ability to turn on to grip, and turn off to ungrip. The gripper will be used by the robot arm to pick up checker pieces, and make its move.
\subsubsection{Source}
Hoang Ho
\subsubsection{Constraints}
Objects may need to have certain magnetic strength to be able to be picked up by the gripper. On the other hand, the gripper magnetic strength may be needed to take into account also, so that checker pieces relative to the one the robot arm is picking up is not picked up either. It may be that we may need to use a different type of gripper for the optimal object pick up motion. We may be limited by the different magnets we can buy whether it be size, strength, or budget. These limitations also apply to the gripper itself.
\subsubsection{Standards}
N/A
\subsubsection{Priority}
Critical

\subsection{The system shall follow the rules of American checkers.}
\subsection{Description}
The checkers engine should be programmed to know how to play by the rules of American checkers (English draughts) to avoid confusion.
\subsection{Source}
Kevin Vu
\subsection{Constraints}
N/A
\subsection{Standards}
N/A
\subsection{Priority}
High

\subsection{The system shall be able to abort and reset mid-match.}
\subsubsection{Description}
For demonstration purposes, the checkers program should be able to abort mid-match to prepare for the next round of tourists/viewers to play or watch a fresh match.
\subsubsection{Source}
Kevin Vu
\subsubsection{Constraints}
N/A
\subsubsection{Standards}
N/A
\subsubsection{Priority}
High

\subsection{The product shall show the state of the game to the player at all times.}
\subsubsection{Description}
This will be used to provide a computerized version of the game.
\subsubsection{Source}
Nimita Uprety
\subsubsection{Constraints}
N/A
\subsubsection{Standards}
N/A
\subsubsection{Priority}
High

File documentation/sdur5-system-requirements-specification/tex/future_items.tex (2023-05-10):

%In this last section, you will reiterate all requirements that are listed as priority 5. This is repetitive, but necessary as a concise statement of features/functions that were considered/discussed and documented herein, but will NOT be addressed in the prototype version of the product due to constraints of budget, time, skills, technology, feasibility analysis, etc. Use the following format for this section.

This section covers the future requirements for the UR5 Checkers-Playing co-bot. These are the further developments that will be potentially made on the project which include but are not limited to having difficulty level setting, UR5 automatically resetting the board, and option to play other regional variations of the robot.

\subsection{The system shall have a difficulty level setting.}
\subsubsection{Description}
The user should be able to select an easier or a harder opponent to face. The difficulty of the opponent could be defined by how many moves ahead the system takes into account, or a particular algorithm.
\subsubsection{Source}
Kevin Vu
\subsubsection{Constraints}
N/A
\subsubsection{Standards}
N/A
\subsubsection{Priority}
Future

\subsection{The system shall be able to automatically reset the board and replace the checkers pieces.}
\subsubsection{Description}
After completing a match or aborting a match, the UR5 robot arm should automatically reset the board and its checker pieces to prepare for the next match.
\subsubsection{Source}
Kevin Vu
\subsubsection{Constraints}
N/A
\subsubsection{Standards}
N/A
\subsubsection{Priority}
Future

\subsection{The system shall have the option to play other regional variations of checkers that use an 8x8 squares board.}
\subsubsection{Description}
Since there are many different variations of checkers played around the world (Russian draughts, Turkish draughts, etc.), there is a possibility to program the robot to play by slightly different rules.
\subsubsection{Source}
Kevin Vu
\subsubsection{Constraints}
N/A
\subsubsection{Standards}
N/A
\subsubsection{Priority}
Future

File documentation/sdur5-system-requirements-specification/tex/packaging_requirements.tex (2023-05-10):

% Include a header paragraph here. Packaging requirements are those requirements that identify how the delivered product will be packaged for delivery to the end-user; or how it will "look" when finished and delivered. For example, you might specify that the software required for operation will be pre-loaded on the hard drive, delivered on CD/DVD, or available via download. Software might be customer installable, or not, etc. Hardware components could be all in a single package, provided as a "bag of parts" to be assembled/installed by the user, painted a certain color, logos affixed, etc. Care should be taken not to duplicate requirements found in other sections of this document.

% \subsection{Requirement Name}
% \subsubsection{Description}
% Detailed requirement description...
% \subsubsection{Source}
% Source
% \subsubsection{Constraints}
% Detailed description of applicable constraints...
% \subsubsection{Standards}
% List of applicable standards
% \subsubsection{Priority}
% Priority

This section covers the packaging requirements for the UR5 Checkers-Playing co-bot. The software components of the project will be consolidated through a GitHub repository, from which it can be downloaded and set up. The co-bot will be utilizing a CV Software package in conjunction with a camera for computer vision to perform tasks during the checkers game. Along with the robot arm, the product will include a checkers playing board, checkers pieces, and keyboard input to communicate the conclusion of a player's move to the robot.

\subsection{The product source code will be publicly available in a GitHub repository.}
\subsubsection{Description}
A link to the GitHub repository will be provided. As of now, the repository will contain a ReadMe file with instructions on setting up the robot arm.
\subsubsection{Source}
Hoang Ho
\subsubsection{Constraints}
N/A
\subsubsection{Standards}
N/A
\subsubsection{Priority}
High

\subsection{The product shall also consist of the checkerboard and checker pieces.}
\subsubsection{Description}
Alongside the UR5 robot arm, the checkerboard and checker pieces will be needed for the robot and player to play the game.
\subsubsection{Source}
Hoang Ho
\subsubsection{Constraints}
N/A
\subsubsection{Standards}
N/A
\subsubsection{Priority}
Critical

\subsection{The product shall consist of a camera.}
\subsubsection{Description}
The system will need to use a camera to gather data on the game state and utilize computer vision.
\subsubsection{Source}
Hoang Ho
\subsubsection{Constraints}
We will be able to utilize a camera that exists in previous years, thus saving our budget.
\subsubsection{Standards}
N/A
\subsubsection{Priority}
Critical

\subsection{The product shall have player enter input from keyboard.}
\subsubsection{Description}
The system will need input from keyboard to act as a way for the player to communicate they have finished their turn.
\subsubsection{Source}
Hoang Ho
\subsubsection{Constraints}
N/A
\subsubsection{Standards}
N/A
\subsubsection{Priority}
High

\subsection{The system shall use a computer vision software package.}
\subsubsection{Description}
The system will need to use a tool for computer vision such as OpenCV.
\subsubsection{Source}
Hoang Ho
\subsubsection{Constraints}
N/A
\subsubsection{Standards}
N/A
\subsubsection{Priority}
Critical

\subsection{The system shall use Python 3.}
\subsubsection{Description}
While programming the robot and implementing computer vision for the application, the Python 3 programming language will be used.
\subsubsection{Source}
Joanna Huynh
\subsubsection{Constraints}
N/A
\subsubsection{Standards}
PEP8 Guidelines will be followed for Python3.
\subsubsection{Priority}
High

\subsection{The product shall come with an informative poster detailing the rules of American checkers.}
\subsubsection{Description}
There should be a poster to display the checkers for players/tourists who are unfamiliar with the rules of American checkers rules to avoid confusion.
\subsubsection{Source}
Kevin Vu
\subsubsection{Constraints}
The poster should be large enough to be legible for a group of tourists to read. It should also be able to be easily attached and detached from the UR5 robot stand.
\subsubsection{Standards}
N/A
\subsubsection{Priority}
Moderate

\subsection{The product shall have a storage box to store away its components and attachments when not in use.}
\subsubsection{Description}
Since the robot arm has multiple uses, it will not always be used as a checkers-playing robot. The pieces and attachments for the robot arm should have a container for storage purposes in order to not lose any pieces.
\subsubsection{Source}
Kevin Vu
\subsubsection{Constraints}
N/A
\subsubsection{Standards}
N/A
\subsubsection{Priority}
High

\subsection{The robot shall remain on its designated red toolbox.}
\subsubsection{Description}
The robot will conduct all checkers games while stationed on the portable red toolbox.
\subsubsection{Source}
Joanna Huynh
\subsubsection{Constraints}
N/A
\subsubsection{Standards}
The toolbox must be transported to specific destinations for demonstrations.
\subsubsection{Priority}
High

\subsection{The camera shall be mounted on a tall tripod and connected via a standard USB port.}
\subsubsection{Description}
This camera will be used to capture the robot's movement.
\subsubsection{Source}
Nimita Uprety
\subsubsection{Constraints}
N/A
\subsubsection{Standards}
N/A
\subsubsection{Priority}
High

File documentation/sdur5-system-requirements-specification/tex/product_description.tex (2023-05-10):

% This section provides a description of your product and defines it's primary features and functions. The purpose is to give the document reader/reviewer enough information about the product to allow them to easily follow the specification of requirements found in the remainder of the document. Your header for this section should introduce the section with a brief statement such as: "This section provides the reader with an overview of X. The primary operational aspects of the product, from the perspective of end users, maintainers and administrators, are defined here. The key features and functions found in the product, as well as critical user interactions and user interfaces are described in detail." Using words, and pictures or graphics where possible, specify the following:

This section provides the reader with an overview of our Checkers-Playing UR5 Co-Bot product. The primary operational aspects of the product from the perspective of end users \& maintainers, are defined here. The key features \& functions found in the product, as well as critical user interactions are described in detail.

\subsection{Features \& Functions}
% What the product does and does not do. Specify in words what it looks like, referring to a conceptual diagram/graphic (Figure X).  Define the principle parts/components of the product. Specify the elements in the diagram/graphic that are part(s) of this product as well as any associated external elements (e.g., the Internet, an external web server, a GPS satellite, etc.)
Our programmed UR5 co-bot is intended to have the following features and functions as outlined in Figure 1:
\begin{itemize}
  \item UR5 Robot Arm: core element of the product that is a programmable Universal Robots Arm with a 5 kg payload.
  \begin{itemize}
      \item Camera: 3D camera that will be mounted to a tall tripod to view the board and analyze it.
      \item Electropermanent Magnet Attachment: will allow the robot arm to pick up pieces individually by turning on the magnet \& then place the pieces by turning off the magnet.
  \end{itemize}
  \item Checker Board \& Pieces: these game pieces will be fundamental to the product as they are what will allow the game-play between the UR5 bot and human user to take place.
  \item Tablet: UR+ Teach Pendant device that will be used to control the robot step by step
  \item Control Box: OEM Control Box that not only powers the UR5 co-bot but also allows for integration with external devices.
  \item Keyboard: Input from the keyboard that will allow the user to notify the robot when they have completed their turn.
  \item Piece Collection Box: Would ideally sit on the table next the the checkers board to allow both the human user and the co-bot to place pieces they have "won".
  \item Monitor: Will display the computerized version of the current state of the board.
\end{itemize}

\subsection{External Inputs \& Outputs}
% Describe critical external data flows. What does your product require/expect to receive from end users or external systems (inputs), and what is expected to be created by your product for consumption by end users or external systems (outputs)? In other words, specify here all data/information to flow into and out of your systems. A table works best here, with rows for each critical data element, and columns for name, description and use.
Given the nature of our project there is only a single external data flow. Our UR5 Co-bot is expected to receive input from end users via the keyboard input that they will press upon completion of their turn, thus signalling the robot to play their next move.

\subsection{Product Interfaces}
% Specify what all operational (visible) interfaces look like to your end-user, administrator, maintainer, etc. Show sample/mocked-up screen shots, graphics of buttons, panels, etc. Refer to the critical external inputs and outputs described in the paragraph above.

Our product will have a simple computerized version this is intended to show the current location of each players pieces.

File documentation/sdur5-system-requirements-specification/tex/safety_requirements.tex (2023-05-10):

% Include a header paragraph specific to your product here. Safety requirements might address items specific to your product such as: no exposure to toxic chemicals; lack of sharp edges that could harm a user; no breakable glass in the enclosure; no direct eye exposure to infrared/laser beams; packaging/grounding of electrical connections to avoid shock; etc.

This section covers the safety precautions surrounding the Checkers-Playing UR5 Co-bot. While working in the laboratory, the team will be following LOTO procedures and NEC wiring compliance. More specific to the robotic arm are standards related to having a designated area for any robotic manipulators, functions that automatically stop the movement of the robotic arm in the case of a collision, and a physical emergency stop button which also halts movement. 

\subsection{Laboratory equipment lockout/tagout (LOTO) procedures}
\subsubsection{Description}
Any fabrication equipment provided used in the development of the project shall be used in accordance with OSHA standard LOTO procedures. Locks and tags are installed on all equipment items that present use hazards, and ONLY the course instructor or designated teaching assistants may remove a lock. All locks will be immediately replaced once the equipment is no longer in use.
\subsubsection{Source}
CSE Senior Design laboratory policy
\subsubsection{Constraints}
Equipment usage, due to lock removal policies, will be limited to availability of the course instructor and designed teaching assistants.
\subsubsection{Standards}
Occupational Safety and Health Standards 1910.147 - The control of hazardous energy (lockout/tagout).
\subsubsection{Priority}
Critical

\subsection{National Electric Code (NEC) wiring compliance}
\subsubsection{Description}
Any electrical wiring must be completed in compliance with all requirements specified in the National Electric Code. This includes wire runs, insulation, grounding, enclosures, over-current protection, and all other specifications.
\subsubsection{Source}
CSE Senior Design laboratory policy
\subsubsection{Constraints}
High voltage power sources, as defined in NFPA 70, will be avoided as much as possible in order to minimize potential hazards.
\subsubsection{Standards}
NFPA 70
\subsubsection{Priority}
Critical

\subsection{RIA robotic manipulator safety standards}
\subsubsection{Description}
Robotic manipulators, if used, will either housed in a compliant lockout cell with all required safety interlocks, or certified as a "collaborative" unit from the manufacturer.
\subsubsection{Source}
CSE Senior Design laboratory policy
\subsubsection{Constraints}
Collaborative robotic manipulators will be preferred over non-collaborative units in order to minimize potential hazards. Sourcing and use of any required safety interlock mechanisms will be the responsibility of the engineering team.
\subsubsection{Standards}
ANSI/RIA R15.06-2012 American National Standard for Industrial Robots and Robot Systems, RIA TR15.606-2016 Collaborative Robots \cite{UR5manual}
\subsubsection{Priority}
Critical

\subsection{The system shall stop upon collision.}
\subsubsection{Description}
When someone collides with the robot arm while it is in motion, the robot arm will automatically stop upon collision rather than continuing its motion. The system keeping track of the game state will also be paused, until explicitly told to resume.
\subsubsection{Source}
Hoang Ho
\subsubsection{Constraints}
N/A
\subsubsection{Standards}
Safety-related functions and interfaces built into the UR5 robots are monitored in accordance to EN ISO13849-1:2008 \cite{UR5manual}
\subsubsection{Priority}
Critical

\subsection{The system shall have an emergency stop.}
\subsubsection{Description}
The UR5 robotic arm has a controller which provides an emergency stop button to immediately stop all robot motion.
\subsubsection{Source}
Joanna Huynh
\subsubsection{Constraints}
N/A
\subsubsection{Standards}
Safety-related functions and interfaces built into the UR5 robots are monitored in accordance to EN ISO13849-1:2008
\subsubsection{Priority}
High

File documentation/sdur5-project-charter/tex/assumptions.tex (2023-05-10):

The following list contains critical assumptions related to the implementation and testing of the project:

\begin{itemize}
    \item Access to the UR5 Robot Arm will be available when needed for implementation and testing
    \item The UR5's controller box will be available and able to connect to a computer through an Ethernet cable
    \item A stable, large space with ample power, network connectivity, and enough lighting will be available for the project to reside in
    \item A gripper for the robot arm will be acquired by the 3rd sprint cycle
    \item A working camera for detection and sensing the game board will be acquired by the 3rd sprint cycle
\end{itemize}

% An assumption is a belief of what you assume to be true in the future. You make assumptions based on your knowledge, experience or the information available on hand. These are anticipated events or circumstances that are expected to occur during your project's life cycle.

% Assumptions are supposed to be true but do not necessarily end up being true. Sometimes they may turn out to be false, which can affect your project significantly. They add risks to the project because they may or may not be true. For example, if you are working on an outdoor unmanned vehicle, are you assuming that testing space will be available when needed? Are you relying on an external team or contractor to provide a certain subsystem on time? If you are working at a customer facility or deploying on their computing infrastructure, are you assuming you will be granted physical access or network credentials?

% This section should contain a list of at least 5 of the most critical assumptions related to your project. For example:

% The following list contains critical assumptions related to the implementation and testing of the project.

% \begin{itemize}
%   \item A suitable outdoor testing location will be available by the 3rd sprint cycle
%   \item The X sensing system developed by Sensor Consulting Company will be delivered according to specifications by the 4th sprint cycle
%   \item Access to the customer installation site will be provided by the 5th sprint cycle
%   \item The customer will provide ample power and network connectivity at the installation site
%   \item The installation site network infrastructure will allow TCP network traffic on port 8080
% \end{itemize}

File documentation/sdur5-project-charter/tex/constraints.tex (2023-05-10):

The following listed items are the projected constraints imposed on the checkers playing UR5 co-bot arm project:

\begin{itemize}
    \item The final prototype demonstration must be completed by May 1st, 2022.
    \item Total development costs for tools, hardware components, and 3D printing must not exceed \$800.
    \item The UR5 co-bot is located at a specific site, so access to it may be restricted by certain business hours. Additionally, programming and testing for robot is less flexible.
    \item Team members have minimal knowledge with computer vision and mechanical components, such as cameras, sensors, and grippers.
    \item Depending on the gripper type for the co-bot arm, a customized checkers board and pieces will have to be created.
    \item There is one co-bot arm for all members to work with.
    \item The UR5 co-bot may need specific lighting in the area that the checkers game is being played in order to adequately detect the pieces. 
    
\end{itemize}

% commented out the instructions using iffalse and fi
\iffalse
Constraints are limitations imposed on the project, such as the limitation of cost, schedule, or resources, and you have to work within the boundaries restricted by these constraints. All projects have constraints, which are defined and identified at the beginning of the project.

Constraints are outside of your control. They are imposed upon you by your client, organization, government regulations, availability of resources, etc. Occasionally, identified constraints turn out to be false. This is often beneficial to the development team, since it removes items that could potentially affect progress.

This section should contain a list of at least 5 of the most critical constraints related to your project. For example:

The following list contains key constraints related to the implementation and testing of the project.

\begin{itemize}
  \item Final prototype demonstration must be completed by May 1st, 20XX
  \item The customer will provide no more than two maintenance personnel to assist in on-site installation
  \item Customer installation site will only be accessible by development team during normal business hours
  \item Total development costs must not exceed \$800
  \item All data obtained from customer site must be reviewed and approved for release by the Information Security Office prior to being copied to any internet connected storage medium
\end{itemize}
\fi

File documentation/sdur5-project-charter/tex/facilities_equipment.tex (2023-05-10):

% What lab space, testing grounds, makerspaces, etc. will you need to complete the project? Will you require any specific equipment, and if so, where will you get it (borrow, lease, purchase, outsource, already present in the lab, etc.). This section should occupy 1/2 page.

For our project we expect to be primarily utilizing the senior design lab facilities located in ERB 335 as this is where the UR5 Robot Arm should be stored throughout the majority of the year. This space will also be utilized by our team for the development, testing and implementation of any components we add to our project such as the camera and checker piece gripper. That said, the co-bot is currently being used on other projects and is not present in the senior design lab at the moment. The UR5 arm is expected to return to the ERB 335 lab soon but its final location is subject to change.

Given that our team is still undecided on what kind of gripper we will be implementing to pick up our checkers pieces we may or may not have an additional facility that we use. This is due to the fact that we are currently exploring two options, a vacuum gripper and an electropermanent magnetic one. If our team decides to make the gripper accessory magnetic, this means we will also need to 3D print our own checkers pieces so that we can put magnets inside them. In the event that we choose this option then we will utilize the available 3D printers in the FabLab to build our custom game pieces.

In terms of equipment the most vital piece is the UR5 Robot Arm itself. This piece will be leased from the College of Engineering at the University of Texas at Arlington. Additional equipment items include 3D printers (located in the FabLab) \& design software, Robot Operating Software [ROS]. However due to the complexity of our project this is not a final list of equipment pieces as we may need to use additional items to create our gripper accessories \& checkers pieces.

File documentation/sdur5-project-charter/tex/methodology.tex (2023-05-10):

% This is the "What" of the project and it states what will be done to address the problem statement. This section should focus mostly on what your solution is going to be and what it is going to do (i.e., we are going to build an app, robot, device, etc. to perform some task which mitigates the problem). If someone were to ask you \textit{"What are you doing for your senior design project?"}, this is section is basically what you would tell them.

Our project's objective is to program the UR5 co-bot to play checkers against a human opponent. We aim to accomplish this by utilizing computer vision to analyze the current state of the board so that the co-bot can then make an educated choice as to which move to play next. In order to pick up each individual piece we will create an accessory that we will attach to the UR5 arm so that the checkers pieces can either be picked up by vacuum suction or through electropermanent magnetism. The robot and the human player will take turns moving pieces until one of them wins.

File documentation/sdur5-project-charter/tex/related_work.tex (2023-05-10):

% Discuss the state-of-the-art with respect to your product. What solutions currently exist, and in what form (academic research, enthusiast prototype, commercially available, etc.)? Include references and citations as necessary using the \textit{cite} command, like this \cite{Rubin2012}. If there are existing solutions, why won't they work for your customer (too expensive, not fast enough, not reliable enough, etc.). This section should occupy 1/2 - 1 full page, and should include at least 5 references to related work. All references should be added to the \textit{.bib} file, fully documented in IEEE format, and should appear in the \textit{references} section at the end of this document (the IEEE citation style will automatically be applied if your reference is properly added to the \textit{.bib} file).

% ProTip: Consider using a citation manager such as Mendeley, Zotero, or EndNote to generate your \textit{.bib} file and maintain documentation references throughout the life cycle of the project.

%Štip

Our team discovered several different projects that had components that were similar to our UR5 checkers playing robot project. These projects range from applications in academic research to personal robotics projects. Several of these implementations also explore different technology applications such as speech recognition or magnetic sensors. These differences shed light on the various routes that can be taken to best implement the goal of interactively playing checkers through computer vision. Our team hopes to conceive an interactive demonstration of the UR5 robotic arm's capabilities in a similar vein to these related projects.

One of these existing projects we had stumbled across is the Automated Chess Playing Robot Manipulator by Angelkov et al. \cite{Angelkov2015}. These researchers in the Faculty of Computer Science at Goce Delcev University of Stip were able to successfully implement chess rules to a robot arm that could evaluate board position during a match. This project was also very successful in the aspect of computer vision and robot arm precision. From this project, although we are not programming the robot arm to play chess, we might still be able to learn from their computer vision and robotic arm movement implementation. We would prefer to stick to checkers over chess for a public demonstration, since the rules are simpler and it would be more accessible as a demonstration to the public.

Another existing project of the UR5 robotic arm engaging in a game of chess is the Voice Controlled Chess Robot \cite{Ard2020}. This project by William Ard uses speech recognition for translating recognizable vocal commands into the Cartesian coordinates of the chess board. The Python programming language is used to track the board and direct the robotic arm to pick up the chess pieces with a Hand-E gripper and move it across the board. While this project does not involve computer vision, our project may gain inspiration from the algorithms used to coordinate the pieces, but will also integrate machine and computer vision via a camera to  accurately target the chess pieces. This is also because we lack the speech recognition aspect, so our robotic arm must have a source that allows it to understand the state of the board.  

Another project we had seen was a checkers computer vision and move suggestion robot by Alex Thiele \cite{Thiele2015}. This project had successfully implemented robot computer vision and checkers rules. In this project, Thiele implemented a robotic arm to pick and place a checker piece. The robotic arm was equipped with a camera which scanned the board, calculated the new position of the checker piece, and picked and placed the piece in its new position. In our project, we would like to combine checkers, robotics, artificial intelligence, and interactivity to produce a memorable demonstration for prospective students.

The Interactive Robot for Playing Russian Checkers by Kopets et al \cite{Kopets2020}. uses a different type of robotic arm called the 3 Degree of Freedom (3-DOF) Dobot robotic arm in conjunction with Hall sensors. The purpose of the Hall sensors is to avoid using computer vision. The team did not want to use computer vision due to potential complications with light sensitivity and calibration. Instead, the Hall sensors are used to sense if a checker piece is on a specific part of the board. In addition to this, the robotic arm has a limited working space, so the checkers playing board is a custom compact size of 15 cm X 15 cm. This project explores an important aspect of the disadvantages of computer vision. Because our UR5 project will be using computer vision, there will be certain constraints to account for in order to avoid complications such as light sensitivity.  

A more broadly related study is a proposed approach regarding a robot's ability to learn to pick and place objects by Mohammed et al. \cite{Mohammed2021}. The study proposes an effective strategy to pick and place to a new location that focuses on manipulating objects in cluttered environments. The experiments described in this paper details a UR5 co-bot arm, equipped with a Parallel-jaw gripper, which learns to detect the best grasping points of objects through trial and error. The project used Q-network learning method and RGB-D images. Similarly to this study, our project will include pieces that are in a semi-cluttered environment because the checker pieces will be relatively close together. The sensor and camera on the UR5 co-bot arm will need to be able to detect the correct positions and IDs of the checker pieces in order to move them to new positions. In contrast, our project will be using a magnetic gripper, and there will be no variance in the shape and size of the targeted objects that are being picked and placed.

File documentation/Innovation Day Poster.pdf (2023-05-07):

2023 UTA College of Engineering Innovation Day | April 18, 2023
- UR5 co-bot: The robot is connected to the computer and utilizes the minimax algorithm to make game decisions.

Ho, H., Huynh, J., Rojas, P., Uprety, N., Vu, K.

# Checkers-Playing UR5 Co-Bot

Executive Summary | Experimental Setup

### Background

The UR5 collaborative robot (co-bot) belonging to the Computer Science and Engineering department at the University of Texas at Arlington currently does not showcase the collaborative nature of its ability to interact closely with humans. The co-bot has been programmed to perform an interactive game of Checkers, the strategy board game, against a human opponent safely and intelligently.

The purpose of the checkers-playing co-bot project is to present the co-bot to prospective College of Engineering students for marketing purposes as well as the opportunity to expose students to industrial automation technology. In addition to this, prospective students will gain exposure to different projects that computer science, software engineering, and computer engineering students get to work with.

Our project aims to showcase how a robot arm can be programmed to play a game of Checkers. Although there is no demand for a checkers-playing robot today, there is a growing demand for engineers in the modern world, especially when it comes to computing technologies. With this project, we hope to ignite new and existing passions for technology and innovation in the students of tomorrow.

Through the use of computer vision, artificial intelligence and the UR5 co-bot, we have given the robot arm the ability to play a game of Checkers against a human player. We accomplished this by utilizing computer vision to analyze the current state of the board so that the co-bot can then use artificial intelligence to make an educated choice as to which move to play next.

- Computer vision allows the detection of the ArUco markers on the Checkers pieces and determines their position on the game board.
- The magnetic gripper accurately moves pieces from one cell to another through the program calculations and signals to the Arduino that controls the magnet.
- The UR5 Robot arm uses artificial intelligence to make optimal game decisions using the minimax algorithm.

### Experimental Test Plan

### Experimental Results

### Conclusions

- First, the game script is run on the computer by the human
player.
- This script will run until one of the players wins the game, or the human decides to quit
early.
- The computer then utilizes the camera to assess the state of the board and will continue to do so throughout the game.
- The human player will be assigned the blue Checkers pieces and play first.

Insights:
- We were able to program the UR5 co-bot to be able to play a complete game of Checkers with a human player with all specifications and constraints met.

Lessons Learned:
- We started out with little knowledge of computer vision, artificial intelligence, electrical components, robotics, and over time, we were able to integrate these disciplinaries into the making of a fully functional interactive game.

Future Plans:
- Potential for UR5 to always win in a game of Checkers against a human player or another robot.
- UR5 can have capabilities to automatically reset the board and replace the Checkers pieces by itself with difficulty level settings.
- UR5 could have the option to play other regional variations of Checkers in the future.

Acknowledgments:
- Special thanks to Dr. Christopher McMurrough and the CSE Department.

## CSE Senior Design

- Magnetic gripper: Allows the robot arm to pick up pieces individually by turning on the electromagnet and placing the pieces by turning off the electromagnet.
- Arduino and MOSFET module: Turn the electromagnet on/off to pick up and drop the pieces. The MOSFET module drives the gripper and listens to the signal from the Arduino.
- RealSense camera: The computer receives and processes the frames from the RealSense D435 camera for piece detection. The library used is OpenCV.
- Checkers pieces: ArUco markers are attached to the top of the 3D printed surface for the identification and detection by the camera.

Figure 3. Conceptual Drawing of Gameplay

Figure 2. Electromagnet Circuit

Figure 1. UR5 Playing Checkers

Figure 6. Marker Detection Figure 7. Arduino and MOSFET module setup

1. Techwithtim. (2020, September 3).“Techwithtim/Python-Checkers-AI/checkers: A checkers AI using the minimax algorithm.” Github, https://github.com/techwithtim/Python-Checkers-AI
2. Lindvig, A. P. (2022, October 31). Ur-rtde. PyPI. Retrieved April 7, 2023, from https://pypi.org/project/ur-rtde/
3. Söderby, K. (2023, March 9). Getting started with Arduino: Arduino documentation.
Arduino Documentation | Arduino Documentation. Retrieved April 7, 2023, from
https://docs.arduino.cc/learn/starting-guide/getting-started-arduino
4. UniversalRobots. (2012). Universal Robots User Manual Version 1.6. Universal Robots
A/S.https://s3-eu-west-1.amazonaws.com/ur-support-site/17958/manual_en_UR5_CB2_1.6_US.pdf. (https://s3-eu-west-1.amazonaws.com/ur-support-site/17958/manual_en_UR5_CB2_1.6_US.pdf.)

### References

- When the human player makes a move, the human must use the computer keyboard to communicate to the computer that they have completed their turn and it is now the UR5’s turn to make a move.
- The computer will communicate with the robot arm and issue commands for it to make a particular move.

Figure 8. Functional
Magnet Gripper

Figure 4. System Overview

Figure 5. AruCo Markers on Checkers pieces

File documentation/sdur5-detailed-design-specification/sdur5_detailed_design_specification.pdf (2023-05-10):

## DEPARTMENT OF COMPUTER SCIENCE & ENGINEERING

## THE UNIVERSITY OF TEXAS AT ARLINGTON

## DETAILED DESIGN SPECIFICATION

# CSE 4317: SENIOR DESIGN II SPRING 2023

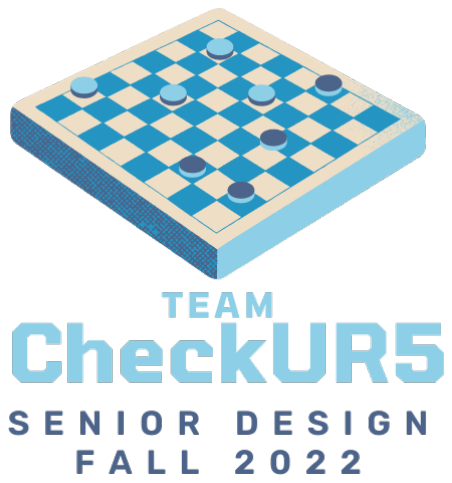
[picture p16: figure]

## TEAM CHECKUR5

## CHECKERS-PLAYING UR5 CO-BOT

NIMITA UPRETY
PATRICIA ROJAS
HOANG HO
KEVIN VU
JOANNA HUYNH
Team CheckUR5 - Spring 2023 | page 1 of 19

REVISION HISTORY

Revision | Date | Author(s) | Description
0.1 | 2.01.2023 | HH | document creation
0.2 | 2.24.2023 | HH, KV, JH, PR, NU | complete draft
0.3 | 2.24.2023 | HH, KV, JH, PR, NU | release candidate 1
0.4 | 5.10.2023 | HH, KV, JH, PR, NU | final draft

CONTENTS

1 Introduction | 5
2 System Overview | 5
3 Computer Layer Subsystems | 6
4 Move Execution Layer Subsystems | 10
5 Move Decision Layer Subsystems | 12
6 External Components Layer Subsystems | 14
7 Appendix A | 17

LIST OF FIGURES

1 | System architecture | | 6
2 | Computer layer subsystems diagram | | 7
3 | Move Execution subsystem description diagram | | 10
4 | Example subsystem description diagram | | 12
5 | External components subsystem description diagram | | 14
6 | CAD Model of our Magnetic Gripper Attachment | | 17
7 | CAD Model of our Regular Checkers Pieces | | 17
8 | CAD Model of our King Checkers Pieces | | 17
9 | Schematic View of our Arduino & Electromagnet setup | | 18
10 | Circuit View of our Arduino & Electromagnet setup | | 19

LIST OF TABLES

### 1 INTRODUCTION

The UR5 co-bot will be programmed to be able to play the interactive & strategy-based game, checkers, against a human opponent. The robot will have an electropermanent magnetic attachment that will allow it to pick up and move the individual checkers pieces. The robot is not intended to beat the human opponent every time but rather just have the ability to play a full game of checkers against them. Our project aims to showcase the UR5 co-bot’s abilities as a means of promoting the UT Arlington College of Engineering to prospective students through the means of an interactive demonstration.

### 2 SYSTEM OVERVIEW

The system for our product is currently simplified into 4 layers and 3 high-level components. Each layer/component will interact with one another in different ways.

The Opponent is the person that will be going against the robot during the checkers game. The Input Device is one of the ways the opponent will be able to facilitate the progression of the checkers match. The camera is the component that acts as the eyes into the real world for our system. The Move Decision layer is the layer that will make all of the move decisions that the robot will make. This layer consists of Computer Vision and AI. The Computer layer is the central piece of our system. This layer acts as the facilitator of the checkers match, and receives input from the Opponent to progress the match, sends signals to the AI layer to grab board state and make a move, and signals the UR5 Robot Arm layer to execute those moves. The Move Execution layer is the layer that will physically execute the moves that our system will make during a checkers match with the robot arm and related parts. And finally, The External Components layer is composed of all of the physical checkers board game pieces. Both the Opponent component and the Move Execution layer physically interact with the External Components layer when they have made their move decisions to progress the match.


Figure 1: System architecture

### 3 COMPUTER LAYER SUBSYSTEMS

In this section, the Computer layer is described in detail. This layer consists of the HUD, GUI, and Software subsystems. Overall, the layer is responsible for communicating with the players information about the state of the game, sending the robot arm the actions it needs to take, and handling the decisions after each move.

### 3.1 LAYER HARDWARE

The major hardware component of this layer is the computer itself. This computer is communicating to the UR5 robot arm through an Ethernet cable connected to the same router as the Ethernet cable connected to the UR5 control box. Additionally, as part of the computer, a monitor to display information to the player. A USB is also required to send to the Arduino the source code written to control the magnetic gripper.

### 3.2 LAYER OPERATING SYSTEM

The layer requires Linux distribution Ubuntu 22.04 LTS.

### 3.3 LAYER SOFTWARE DEPENDENCIES

The layer will use the Python 3.10.6 programming language. It will also need to use the Arduino programming language to write the code to be executed on the Arduino that controls the magnetic gripper. Additionally, it is dependent on the Move Decision layer.

### 3.4 HUD SUBSYSTEM

The Heads-Up Display (HUD) subsystem is a class that communicates with the Software subsystem of the Computer layer to receive information about the status of the game.The HUD subsystem displays to the user the status of the game and any information needed for the user. In this case the user is the Opponent layer. Information on the status of the game includes the current scores and a display of the game board on the computer monitor. This information is provided by the Software subsystem. Each time a player overtakes another player’s checker piece, the score will be updated. When the physical game board changes, such as when a player moves a piece, this will also be reflected on the screen through the HUD.


Figure 2: Computer layer subsystems diagram

### 3.4.1 SUBSYSTEM HARDWARE

A monitor connected to the computer to display game state status to the player.

### 3.4.2 SUBSYSTEM SOFTWARE DEPENDENCIES

This subsystem is dependent on the Software subsystem to receive information about the status of the game to display. It will also have software dependencies on GUI libraries such as PyQt5 or Tkinter.

### 3.4.3 SUBSYSTEM PROGRAMMING LANGUAGES

The subsystem uses Python 3.10.6 as the programming language used.

### 3.4.4 SUBSYSTEM DATA STRUCTURES

N/A

### 3.4.5 SUBSYSTEM DATA PROCESSING

N/A

### 3.5 GUI SUBSYSTEM

The Graphical User Interface (GUI) subsystem is a class that is the main interactive component between the Computer and Opponent layers. It communicates with the Software subsystem within the Computer layer for its inputs and outputs. The GUI displays buttons for the user (Opponent) to interact with. These buttons will be able to change the state of the game for purposes such as new game, restart game, and quit game. Each time the Opponent interacts with the GUI by clicking a corresponding button to a function, that button will send a mouse click signal for that button to the Software subsystem. This signals to the Software subsystem to execute the function associated with the button that is clicked. For example, if the user clicks a new game button, the software executes the processes needed to reset the state of the game and UR5 robot arm.

### 3.5.1 SUBSYSTEM HARDWARE

A monitor connected to the computer to display the different options to the player. A mouse is also required for the player to interact with the GUI.

### 3.5.2 SUBSYSTEM SOFTWARE DEPENDENCIES

This subsystem will have software dependencies on GUI libraries such as PyQt5 or Tkinter.

### 3.5.3 SUBSYSTEM PROGRAMMING LANGUAGES

The subsystem uses Python 3.10.6 as the programming language used.

### 3.5.4 SUBSYSTEM DATA STRUCTURES

N/A

### 3.5.5 SUBSYSTEM DATA PROCESSING

N/A

### 3.6 SOFTWARE SUBSYSTEM

The Software subsystem is the main program for managing the checkers game itself and is behind the actions the UR5 Robot Arm will execute. This subsystem not only includes the source code itself, but also software packages needed for the program. The Software subsystem is responsible for handling events from the GUI. The subsystem also communicates with the UR5 robot arm through the Computer layer. The subsystem handles data on the status of the robot arm received from the robot arm itself. It also communicates to the robot arm what programmed actions it will need to perform. These actions will be determined by its interactions with the Move Decision layer which consists of the AI subsystem. The Software subsystem is also responsible for handling inputs from the Input Button/Device layer through the Computer layer.

### 3.6.1 SUBSYSTEM HARDWARE

N/A

### 3.6.2 SUBSYSTEM SOFTWARE DEPENDENCIES

The Software subsystem requires the ur_rtde interface library to communicate with the UR5 robot arm. This library will allow us to write Python code to receive data from the UR5, and also control it. This is done using the RTDE Receive Interface API and RTDE Control Interface API from the library respectively. Documentation for the library can be found here: https://sdurobotics.gitlab.io/ur_rtde/index.html.

Controlling the UR5 includes communicating with the Move Execution layer and sending the commands to move the robot arm to a certain position. The subsystem is dependent on the Computer Vision and AI subsystems from the Move Decision layer to determine the commands it needs to send to the robot arm. It also needs this dependency to manage the checkers game and send the data required by the HUD subsystem. Moreover, it is also dependent on the GUI subsystem and Input Button/Device layer to listen to events from the player and handle them for the checkers game accordingly.

### 3.6.3 SUBSYSTEM PROGRAMMING LANGUAGES

The subsystem uses Python 3.10.6 as the programming language used.

### 3.6.4 SUBSYSTEM DATA STRUCTURES

N/A

### 3.6.5 SUBSYSTEM DATA PROCESSING

N/A

### 4 MOVE EXECUTION LAYER SUBSYSTEMS

In this section, we describe the move execution layer. This layer is responsible for one of the key functionalities of our project which is the UR5 Robotic Arm’s movement, which allows for the checkers game to take place between the user and the co-bot. The move execution layer is made up of three subsystems, the UR5 Robot Arm itself, the electromagnetic gripper, as well as an Arduino.

### 4.1 LAYER HARDWARE

In terms of the Move Execution Layer the most heavily involved hardware component for this layer is the UR5 robotic arm itself.

### 4.2 LAYER OPERATING SYSTEM

This layer utilizes Robot Operating System (ROS), although we do not primarily use ROS as we are primarily using Python to move our co-bot. ROS will be utilized to check the status of our robot’s arm movements/coordinates at any given time.

### 4.3 LAYER SOFTWARE DEPENDENCIES

This layer will also utilize the Python 3.10.6 programming language.


Figure 3: Move Execution subsystem description diagram

### 4.4 UR5 ROBOT ARM

The UR5 co-bot arm must be able to follow the instructions as asked by the software in order to hover over the correct location on the checker board. The robot must be able to move to fixed locations as predetermined by ROS and our custom software in order to not only move to specified pieces on the board but also to the collection box, and a waiting position.
The UR5 co-bot arm is responsible for the main mechanics of our project. As its ability to move to move to a spot on the board and pick up a piece and move it to another position is necessary so that the

UR5 can play against its human oppponent.
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

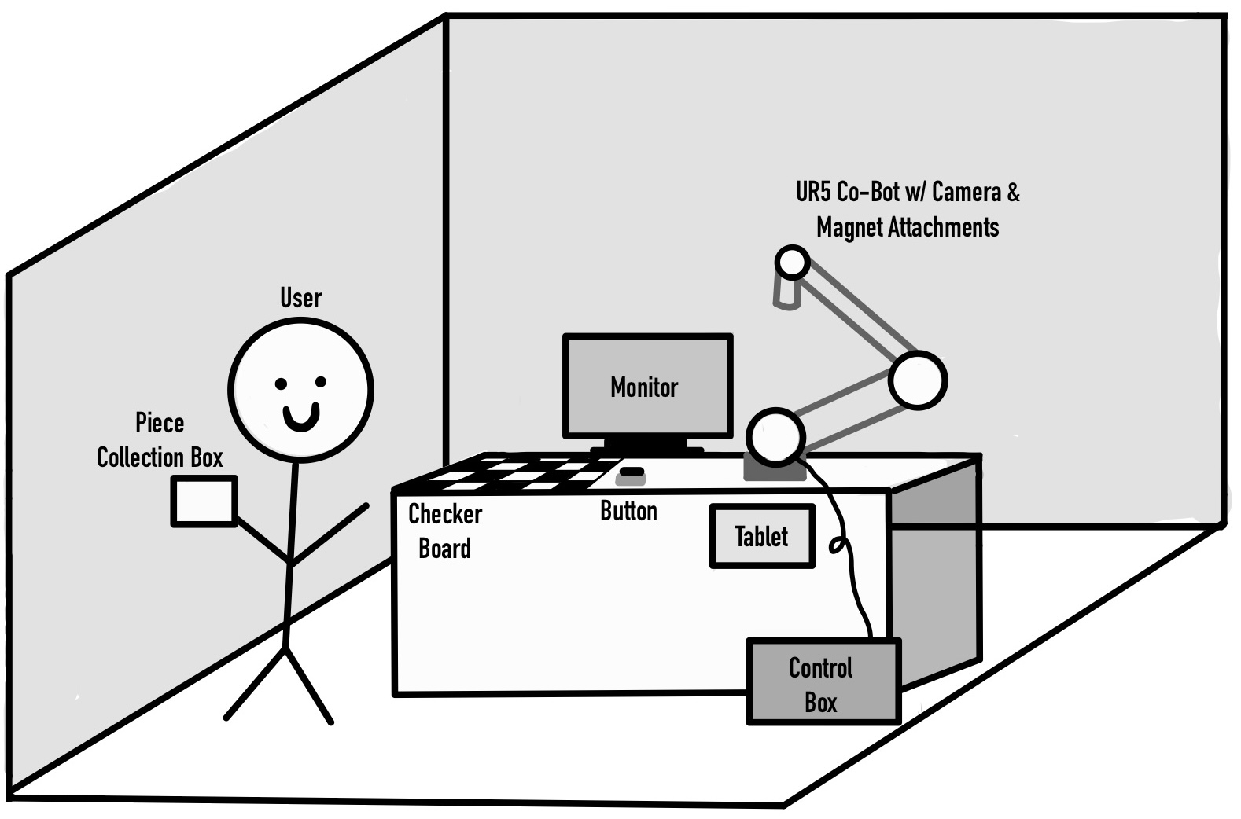
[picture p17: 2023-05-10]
documentation/sdur5-detailed-design-specification/images/Conceptual-Drawing.jpg

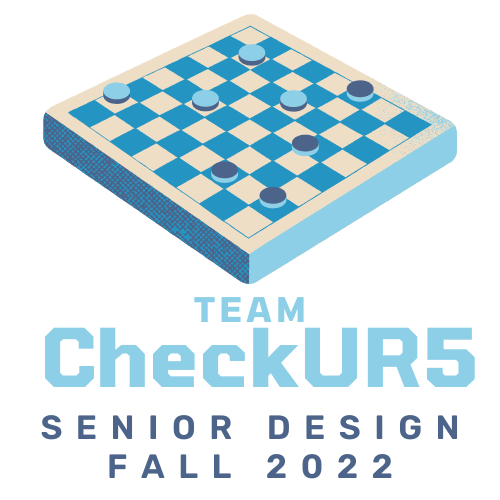
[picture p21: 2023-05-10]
documentation/sdur5-detailed-design-specification/images/Transparent_CheckUR5.png

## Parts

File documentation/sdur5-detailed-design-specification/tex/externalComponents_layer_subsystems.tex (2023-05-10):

In this section, the External Components layer is described in detail. This layer is comprised of the physical parts that make the checkers game, this includes the checkers playing board, the checkers pieces, and the collection box.

\subsection{Layer Hardware}
N/A or The components of this layer do now require any computer system hardware but it deals with the hardware of the checkers game, including the playing board, the checkers pieces, and the collection box.

\subsection{Layer Operating System}
N/A

\subsection{Layer Software Dependencies}
N/A

%%%%%%%%%%%%%%%%%%%%%%%%%%%%%%%%%%%%%%%%%
\subsection{Playing Board}
The Playing Board is the physical wooden platform with distinct cells which the checkers game is played upon. 

\begin{figure}[h!]
	\centering
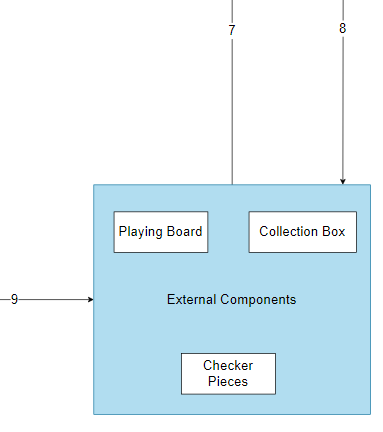
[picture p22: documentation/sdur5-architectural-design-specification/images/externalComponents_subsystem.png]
 	
 \caption{External components subsystem description diagram}
\end{figure}

\subsubsection{Subsystem Hardware}
% A description of any involved hardware components for the subsystem.
N/A

\subsubsection{Subsystem Operating System}
% A description of any operating systems required by the subsystem.
N/A

\subsubsection{Subsystem Software Dependencies}
% A description of any software dependencies (libraries, frameworks, design software for mechanical parts or circuits, etc) required by the subsystem.
N/A

\subsubsection{Subsystem Programming Languages}
% A description of any programming languages used by the subsystem.
N/A

\subsubsection{Subsystem Data Structures}
% A description of any classes or other data structures that are worth discussing for the subsystem. For example, data being transmitted from a microcontroller to a PC via USB should be first be assembled into packets. What is the structure of the packets?
N/A

\subsubsection{Subsystem Data Processing}
% A description of any algorithms or processing strategies that are worth discussing for the subsystem. If you are implementing a well-known algorithm, list it. If it is something unique to this project, discuss it in greater detail.
N/A

%%%%%%%%%%%%%%%%%%%%%%%%%%%%%%%%%%%%%%%%%
\subsection{Checkers Pieces}
The checkers pieces are the focus of the two players as they are the items that will be manipulated during the match. 

\subsubsection{Subsystem Hardware}
N/A

\subsubsection{Subsystem Operating System}
N/A

\subsubsection{Subsystem Software Dependencies}
% A description of any software dependencies (libraries, frameworks, design software for mechanical parts or circuits, etc) required by the subsystem.
N/A

\subsubsection{Subsystem Programming Languages}
% A description of any programming languages used by the subsystem.
N/A

\subsubsection{Subsystem Data Structures}
% A description of any classes or other data structures that are worth discussing for the subsystem. For example, data being transmitted from a microcontroller to a PC via USB should be first be assembled into packets. What is the structure of the packets?
N/A

\subsubsection{Subsystem Data Processing}
% A description of any algorithms or processing strategies that are worth discussing for the subsystem. If you are implementing a well-known algorithm, list it. If it is something unique to this project, discuss it in greater detail.
N/A

%%%%%%%%%%%%%%%%%%%%%%%%%%%%%%%%%%%%%%%%%
\subsection{Collection Box}
The collection box stands off to the side ready to hold the checkers pieces.

\subsubsection{Subsystem Hardware}
% A description of any involved hardware components for the subsystem.
N/A

\subsubsection{Subsystem Operating System}
% A description of any operating systems required by the subsystem.
N/A

\subsubsection{Subsystem Software Dependencies}
% A description of any software dependencies (libraries, frameworks, design software for mechanical parts or circuits, etc) required by the subsystem.
N/A

\subsubsection{Subsystem Programming Languages}
% A description of any programming languages used by the subsystem.
N/A

\subsubsection{Subsystem Data Structures}
% A description of any classes or other data structures that are worth discussing for the subsystem. For example, data being transmitted from a microcontroller to a PC via USB should be first be assembled into packets. What is the structure of the packets?
N/A

\subsubsection{Subsystem Data Processing}
% A description of any algorithms or processing strategies that are worth discussing for the subsystem. If you are implementing a well-known algorithm, list it. If it is something unique to this project, discuss it in greater detail.
N/A

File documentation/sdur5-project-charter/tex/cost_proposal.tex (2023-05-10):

The approximate budget of the project is 800 USD which will be dedicated towards buying a camera, suction cup, magnets, and other materials for the chess board and game. The camera will be necessary for the sensors to detect player movements, the suction cup for the gripper will be used in picking and placing Checkers, the magnet will be needed for sticking the Checkers pieces in place, the Checkers board will be made of birch plywood which will be bought and painted, the paint will be bought and used for the Checkers board, and the Checkers pieces will be 3D printed at the UT Arlington FabLab with the NinjaFlex Filament as the primary material. 

\subsection{Preliminary Budget}
\begin{table}[h]
\begin{center}
\begin{tabular}{ | m{12em} | m{10em}| m{10em} | } 
  \hline
  \textbf{Components} & \textbf{Quantity} & \textbf{Estimate(USD)} \\
  \hline
  Camera & 1 & 200 \\ 
  \hline
  Suction Cup & 1 & 50 \\ 
  \hline
  Magnets & 24 & 15 \\
  \hline
  Birch Plywood Panel (1/4 in. x 1.5 ft. x 1.5 ft.) & 1 & 20 \\ %for checkers board
  \hline
  Paint & 1 & 15 \\
  \hline
  3D Printed Checkers Pieces & 24 & 25 \\
  \hline
\end{tabular}
\caption{Preliminary Budget}
\end{center}
\end{table}
\subsection{Current \& Pending Support}
The default funding source for the project is the CSE Department who will provide 800 dollars for the project.

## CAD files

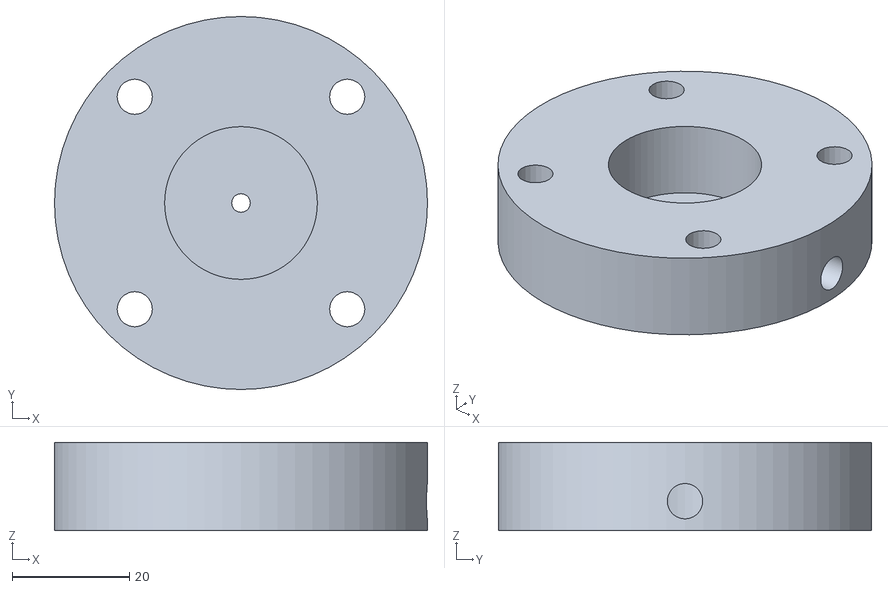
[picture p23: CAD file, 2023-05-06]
designs/gripper-attachment-final.stl
63.5 x 63.5 x 15.0

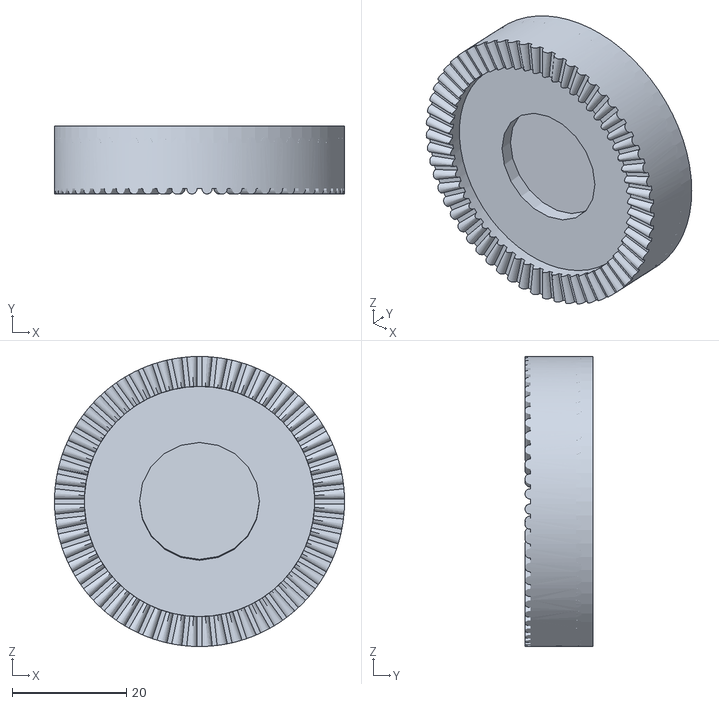
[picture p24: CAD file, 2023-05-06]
designs/checker-piece-final.stl
50.8 x 11.9 x 50.8

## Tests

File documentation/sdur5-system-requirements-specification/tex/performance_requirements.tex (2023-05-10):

%Include a header paragraph specific to your product here. Performance requirements address items such as: how fast specific critical operations must complete; how long it takes to start/stop activities; how long the battery must last; maximum time it must take to set up; etc.

This section covers the performance requirements for the UR5 Checkers-Playing co-bot. This includes how the system will recognize the checkers pieces, recognize its magnetic gripper, complete its turn within a certain time, calculate certain moves ahead, how it will use frames from the webcam, and the way points setup for the robot.

\subsection{The system shall accurately recognize the checkers pieces.}
\subsubsection{Description}
The robotic arm should be able to recognize the custom-made checkers pieces and be able to distinguish between its piece and player's piece to select and grip pieces that are within its domain.
\subsubsection{Source}
Joanna Huynh
\subsubsection{Constraints}
Requires a camera that can detect location.
\subsubsection{Standards}
N/A
\subsubsection{Priority}
Critical

\subsection{The UR5 robotic arm shall recognize when the magnetic gripper should be activated.}
\subsubsection{Description}
The robotic arm's magnetic gripper should only activate once it is its turn in the game, it has decided which piece should be moved, and it has decided on the end location on the checkers board. 
\subsubsection{Source}
Joanna Huynh
\subsubsection{Constraints}
N/A
\subsubsection{Standards}
N/A
\subsubsection{Priority}
High

\subsection{Both the UR5 robotic arm and human user shall complete their turns without a set time limit.}
\subsubsection{Description}
The robotic arm and the player should be able to efficiently complete their turn without a set time limit.
\subsubsection{Source}
Joanna Huynh
\subsubsection{Constraints}
N/A
\subsubsection{Standards}
N/A
\subsubsection{Priority}
Moderate

\subsection{The system shall calculate at least three moves ahead.}
\subsubsection{Description}
This will be used to find the accurate move for the robot arm.
\subsubsection{Source}
Kevin Vu
\subsubsection{Constraints}
N/A
\subsubsection{Standards}
N/A
\subsubsection{Priority}
High

\subsection{The product will have detect ArUco markers detection.}
\subsubsection{Description}
The ArUco markers are used on all Checkers pieces for the program to detect their state on the board.
\subsubsection{Source}
Nimita Uprety
\subsubsection{Constraints}
N/A
\subsubsection{Standards}
N/A
\subsubsection{Priority}
High

\subsection{The UR5 robotic arm shall be able to place checkers pieces in a specific location.}
\subsubsection{Description}
The robotic arm should be able to accurately place the checkers piece within a square cell at its center point on the board.
\subsubsection{Source}
Joanna Huynh
\subsubsection{Constraints}
N/A
\subsubsection{Standards}
N/A
\subsubsection{Priority}
Critical

\subsection{The system arm shall be able to make the most optimal decision.}
\subsubsection{Description}
The system should be able to decide on a move that is most optimal to the robotic arm's victory.
\subsubsection{Source}
Joanna Huynh
\subsubsection{Constraints}
How the system decides on the most optimal move may be limited by the algorithm used or how many moves ahead is anticipated.
\subsubsection{Standards}
N/A
\subsubsection{Priority}
High

\subsection{The product shall communicate with the computer to make a particular move.}
\subsubsection{Description}
The computer will be used to issue commands to the robot to make these moves.
\subsubsection{Source}
Nimita Uprety
\subsubsection{Constraints}
N/A
\subsubsection{Standards}
N/A
\subsubsection{Priority}
Critical

\subsection{The product shall perform as many test games as needed.}
\subsubsection{Description}
The product will perform as many games needed to calculate success and failure rates before being handed to the customer.
\subsubsection{Source}
Nimita Uprety
\subsubsection{Constraints}
N/A
\subsubsection{Standards}
N/A
\subsubsection{Priority}
High

\subsection{The robot arm shall be programmed to be able to move to designated squares on the board.}
\subsubsection{Description}
The program will be used to move the robot arm to precise cells on the board on command.
\subsubsection{Source}
Nimita Uprety
\subsubsection{Constraints}
N/A
\subsubsection{Standards}
N/A
\subsubsection{Priority}
High

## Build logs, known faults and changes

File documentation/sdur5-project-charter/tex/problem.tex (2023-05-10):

The UR5 collaborative robot (co-bot) belonging to the Computer Science department at the University of Texas at Arlington currently does not showcase the collaborative nature of its ability to interact closely with humans. The UR5 co-bot will be programmed to perform a complete game of the strategy board game, checkers, against a human opponent. The purpose of the UR5 co-bot project is to use the programmed co-bot as a marketing strategy for UT Arlington to expose students to industrial automation technology, introduce students to the UT Arlington College of Engineering and Computer Science Engineering departments, and provide an enjoyable educational experience. 

%The problem statement defines the "Why" of the project. This is the higher purpose, or the reason for the project's existence. This section should avoid mentioning implementation details, and focus more on what the current problem is and what would be gained if the problem were to be solved. In short, the is the reason that you are going to be working on something, not the method(s) that you will be employing.

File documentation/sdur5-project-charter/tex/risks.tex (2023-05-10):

% This section should contain a list of at least 5 of the most critical risks related to your project. Additionally, the probability of occurrence, size of loss, and risk exposure should be listed. For size of loss, express units as the number of days by which the project schedule would be delayed. For risk exposure, multiply the size of loss by the probability of occurrence to obtain the exposure in days. For example:

The following high-level risk census contains identified project risks with the highest exposure. Mitigation strategies will be discussed in future planning sessions.

\begin{table}[h]
\resizebox{\textwidth}{!}{
\begin{tabular}{|l|l|l|l|}
\hline
 \textbf{Risk description} & \textbf{Probability} & \textbf{Loss (days)} & \textbf{Exposure (days)} \\ \hline
 Availability of UR5 robot arm due to occupation on other projects  & 0.35 & 14 & 4.9 \\ \hline
 3D printed checkers pieces do not suction properly with robot & 0.40 & 9 & 3.6 \\ \hline
 UR5 robot arm out of commission due to broken components  & 0.25 & 14 & 3.5 \\ \hline
 Unexpected delays on shipping and delivery of parts & 0.10 & 20 & 2.0 \\ \hline
 Custom checkers playing board is incompatible in gameplay & 0.15 & 10 & 1.5 \\ \hline
\end{tabular}}
\caption{Overview of highest exposure project risks} 
\end{table}

% \begin{table}[h]
% \resizebox{\textwidth}{!}{
% \begin{tabular}{|l|l|l|l|}
% \hline
%  \textbf{Risk description} & \textbf{Probability} & \textbf{Loss (days)} & \textbf{Exposure (days)} \\ \hline
%  Availability of X sensor module due to contractor delay  & 0.50 & 20 & 10 \\ \hline
%  Outdoor testing grounds are not available  & 0.20 & 14 & 2.8 \\ \hline
%  Internet access not available at installation site  & 0.30 & 9 & 2.7 \\ \hline
%  Delays in shipping from overseas vendors  & 0.10 & 20 & 2.0 \\ \hline
%  Certification delays at compliance testing facility & 0.15 & 10 & 1.5 \\ \hline
% \end{tabular}}
% \caption{Overview of highest exposure project risks} 
% \end{table}

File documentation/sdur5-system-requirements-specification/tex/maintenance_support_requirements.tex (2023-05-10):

% Include a header paragraph specific to your product here. Maintenance and support requirements address items specific to the ongoing maintenance and support of your product after delivery. Think of these requirements as if you were the ones who would be responsible for caring for customers/end user after the product is delivered in its final form and in use "in the field". What would you require to do this job? Specify items such as: where, how and who must be able to maintain the product to correct errors, hardware failures, etc.; required support/troubleshooting manuals/guides; availability/documentation of source code; related technical documentation that must be available for maintainers; specific/unique tools required for maintenance; specific software/environment required for maintenance; etc.

% \subsection{Requirement Name}
% \subsubsection{Description}
% Detailed requirement description...
% \subsubsection{Source}
% Source
% \subsubsection{Constraints}
% Detailed description of applicable constraints...
% \subsubsection{Standards}
% List of applicable standards
% \subsubsection{Priority}
% Priority

After the delivery of our checkers-playing program for the UR5 robotic arm, the customer will need to maintain the hardware and software in case our product were to ever fail. Since we will be using Commercial Off The Shelf components such as the UR5 robotic arm itself, we will include official documents for those components along with our own source code, documentation, and contact information.

\subsection{The product source code documentation will be available.}
\subsubsection{Description}
Documentation for the source code will be accessible for the customer in case of technical issues or modifications needed.
\subsubsection{Source}
Hoang Ho
\subsubsection{Constraints}
Most of the programming done for the robot arm's movements may be done on the UR5 controller box interface. The programs made here may not be able to be exported.
\subsubsection{Standards}
N/A
\subsubsection{Priority}
High

\subsection{The official UR5 user manual will be available.}
\subsubsection{Description}
The official user manual for the UR5 robot arm will be provided to the customer.
\subsubsection{Source}
Hoang Ho
\subsubsection{Constraints}
N/A
\subsubsection{Standards}
N/A
\subsubsection{Priority}
High

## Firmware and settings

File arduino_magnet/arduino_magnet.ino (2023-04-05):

//define pins, pin values & serial monitor strings

String MAGNET_ON = "Magnet ON";
String MAGNET_OFF = "Magnet OFF";

int MAGNET_PIN = 2;
int magnet_val;

//the setup function runs once when you press rest or power to board
void setup(){
    //initialize MAGNET_PIN as an output
    pinMode(MAGNET_PIN, OUTPUT);

    //start the serial monitor
    Serial.begin(9600);
}

//the loop functions runs over and over again forever
void loop(){
    //read magnet pin input
    magnet_val = digitalRead(MAGNET_PIN);

    //check to see if arduino has recieved any messages & respond accordingly
    if(Serial.available() > 0)
    {
        //read in request
        String message = Serial.readString();
        message.trim(); //get rid of any whitespace at end of string

        //turn magnet on or off depending on message

        if(message == MAGNET_ON)
        {
            digitalWrite(MAGNET_PIN,HIGH); //turn the electromagnet on (HIGH Is the voltage level)   
        }
        else if(message == MAGNET_OFF)
        {
            digitalWrite(MAGNET_PIN,LOW); //turn the electromagent off by making the voltage LOQ
        }
    }

    
    // send messages to the PC indicating status of the magnet
    if(magnet_val == HIGH)
    {
        Serial.println(MAGNET_ON);
    }
    else
    {
        Serial.println(MAGNET_OFF);
    }
    delay(1000); //delay for 1 second
}

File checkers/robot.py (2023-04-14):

import rtde_control
import rtde_receive
import serial
import time

TOP_LEFT = { "x": 0.79556, "y": -0.22876, "z": 0.015, "rx": 2.394, "ry": -2.011, "rz": 0.053 } # position of A1 square
    
MVMT_DIFF = 0.06378 # the distance between the center points of each square
HOVER_DIFF = 0.030 # the difference in z axis to hover over a piece

# 0.03746

HOME_POS = (0.20425, -0.13615, 0.11250, 1.848, -2.428, 0.086) # robot arm resting/home position
BOX_POS = (0.14225, 0.20481, 0.11250, 3.010, -0.446, 0.135) # collection box position for robot arm to drop pieces to

# robot arm speed and acceleration
SPEED = 1.5 # default 1.0
ACCELERATION = 0.375 # default 0.25

# a robot class that you can create to handle all movements of the robot for the checkers game and also the magnet/arduino communications
# robot arm positions for this class is based off of the Base position
class Robot:    
    def __init__(self, arduino_port='/dev/ttyUSB0', robot_ip="192.168.1.102"):
        # arduino to control the magnet
        self.arduino = serial.Serial(port=arduino_port, baudrate=9600, timeout=0)
        
        # UR5 robot arm interface for controlling and receiving robot arm information
        try:
            self.rtde_c = rtde_control.RTDEControlInterface(robot_ip)
            self.rtde_r = rtde_receive.RTDEReceiveInterface(robot_ip)
        
            if self.rtde_c.isConnected() and self.rtde_r.isConnected():
                print(f"Robot is connected.")
        except:
            print(f"Robot is not connected")
    
    # clean up when we're done with robot
    def __del__(self):
        print("Destructor for Robot called. Closing Arduino port, disconnecting robot and deleting object.")
        self.arduino.close()
        self.rtde_c.stopScript()
        self.rtde_c.disconnect()
        self.rtde_r.disconnect()
    
    # magnet functions
    # send a message to the arduino
    def sendMsg(self, msg):
        print(f"\t\tSending message to Arduino: {msg}")
        self.arduino.write(str.encode(msg))

    # send message to turn magnet on
    def turnMagnetOn(self):
        msg = "Magnet ON"
        self.sendMsg(msg)
        
        # check status of the magnet
        self.check_magnet(msg)
            
    
    # send message to turn magnet off
    def turnMagnetOff(self):
        msg = "Magnet OFF"
        self.sendMsg(msg)
        
        # check status of the magnet
        self.check_magnet(msg)
                
    # check if the magnet has turned on/off based on messages received from the Arduino
    # msg is a string supplied to validated the arduino message received against       
    def check_magnet(self, msg):
        timeout = 10 # timeout after 10 seconds
        
        # wait until magnet is on before leaving the function, timeout after 10 seconds
        start = time.time()
        while True:
            # wait until a message is sent
            if self.arduino.inWaiting() != 0:
                packet = self.arduino.readline()
                received_msg = packet.decode('utf-8')
                received_msg = received_msg.strip("\r\n")
                
                end = time.time()
                time_elapsed = end-start
                time_elapsed = round(time_elapsed, 0)
                
                if received_msg == msg or time_elapsed >= timeout:
                    print(f"\n\t\tReceived message from Arduino: {received_msg}")
                    print(f"\t\tElapsed time since message to turn magnet off sent: {time_elapsed}\n")
                    break;
        
        
    # movement functions
    # target is a tuple (row, col) designating the square position on the board to move to
    # the position is calculated based on the origin position (0,0)/TOP_LEFT
    # return the base position list [x, y, z, rx, ry, rz] of the target 
    def get_position(self, target):
        X = TOP_LEFT["x"]
        Y = TOP_LEFT["y"]
        Z = TOP_LEFT["z"]
        RadX = TOP_LEFT["rx"]
        RadY = TOP_LEFT["ry"]
        RadZ = TOP_LEFT["rz"]

        if target[0] != 0:
            diff = (target[0]) * MVMT_DIFF
            val = ord("A")
            #print(f"X difference: {target[0]}-{val} = {diff}")
            Y += diff
        if target[1] != 0:   
            diff = (target[1]) * MVMT_DIFF
            val = ord("1")
            #print(f"Y difference: {target[1]}-{val} = {diff}")
            X -= diff
        
        new_pos = [X, Y, Z, RadX, RadY, RadZ]
        
        return new_pos

    # check if the robot arm has arrived to the target position before doing any other actions
    def check_arrival(self, target):
        current_pos = self.rtde_r.getActualTCPPose()
        error = 0.0040

        while not ((target[0]-error <= current_pos[0] <= target[0]+error)
            and (target[1]-error <= current_pos[1] <= target[1]+error)):
            current_pos = self.rtde_r.getActualTCPPose()
            print(f"Current Actual TCP Pose: {current_pos}")

        return

    # target is a tuple (row, col) designating the square position on the board to grab the piece
    # go to the target position where robot arm will pick up piece and pick up the piece
    def grab_piece(self, target):
        pos = self.get_position(target)
        
        hover_pos = pos.copy()
        hover_pos[2] += HOVER_DIFF
        
        self.rtde_c.moveL(hover_pos, SPEED, ACCELERATION)
        self.rtde_c.moveL(pos, SPEED, ACCELERATION)
        
        self.check_arrival(pos)
        
        # TURN ON THE MAGNET
        self.turnMagnetOn()

        # raise arm back up
        self.rtde_c.moveL(hover_pos, SPEED, ACCELERATION)
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

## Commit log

2023-03-06 Arduino reciever code added, code still needs to be tweaked a little bit
2023-03-06 Arduino Magnet Demo
2023-03-06 Updated arduino sketch with assigned pins & original demo logic
2023-03-06 Added python to arduino magnet demo
2023-03-22 Add magnet helper file
2023-03-22 Add send magnet message function
2023-03-27 Change magnet functions
2023-04-04 Add robot destructor and magnet checks
2023-04-04 Add check magnet status fn and receive arduino msg
2023-04-05 Moved camera
2023-04-06 moved magnet.py and changed ai_move
2023-04-06 Fix print statements
2023-04-06 update board.py count pieces + kings
2023-04-07 Fix algorithm for 0 pieces
    [game.py, robot.py]
2023-04-07 Fix update board to update piece row, col
    [board.py, game.py, robot.py]
2023-05-06 3d print prototypes
2023-05-07 Remove prototype files
    [checker piece final.stl, gripper attachment final.stl]
2023-05-07 Add 3D printed prototype files
    [checker piece final.stl, gripper attachment final.stl]
2023-05-10 Move design files to new directory
    [checker piece final.stl, gripper attachment final.stl]
2023-05-10 Renamed checker files
    [checker-piece-final.stl]
2023-05-10 Rename design file
    [gripper-attachment-final.stl]
